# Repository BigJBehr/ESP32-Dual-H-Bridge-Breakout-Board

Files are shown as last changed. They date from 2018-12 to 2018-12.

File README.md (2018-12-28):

# ESP32 Dual H Bridge Breakout Board

This project is for an ESP32 Breakout board that was designed to be the brains of your next robot. The features of this board are;

Can accommodate any ESP32 dev kit that has two rows of up to twenty pins on one inch centers.
A place to mount a TB6612FNG dual H bridge DC motor controller daughter board.
A two screw terminal block for each motor connection.
A two screw terminal block and a set of five header pins for Vin & Gnd
Two rows of twenty GPIO breakout pins.
Headers for two HC-SR04 Sonar sensors, with voltage dividers on the Echo output.
A header for connecting to a tri-color, common anode, LED with limiting resistors.
On board 5V, 1A voltage regulator with five header pins for 5V & Gnd.
Four sets of headers for I2C connections with 3.3V & Gnd for each connection.
All components mount on one side of the circuit board.
The physical size of the board is 90mm x 56mm, two sided. This puts it well within the 100mm x 100mm size limits for most board makers low cost prototypes.

The board was designed around the DOIT ESP32 DEVKIT V1 which has two rows of eighteen pins each. Easily cut traces on the backside of the board allow you to separate the dedicated 5V, Gnd and 3.3V pins from their respective buses. Then you can use the pins in these locations as GPIO and using jumpers, connect the 5V, Gnd and 3.3V buses to the appropriate pins on the ESP32 dev kit that you are using.

The board was created using Kicad Ver 4.0.7.

## The files
ESP32_Robot_Bd.zip - This is all of the files needed to have the board fabricated. Send this file to your board manufacturer.

ESP32_Robot_Bd.kicad.pcb   - This is the kicad pcb file.

ESP32_Robot_Bd.net         - This is the kicad generated net file for the pcb.

ESP32_Robot_Bd.pdf         - This is a pdf version of the schematic.

ESP32_Robot_Bd.pro         - This is the kicad project.

ESP32_Robot_Bd.sch         - This is the kicad schematic.

ESP32_Robot_Bd-cache.lib   - This is the cached library. It has any custom library parts.

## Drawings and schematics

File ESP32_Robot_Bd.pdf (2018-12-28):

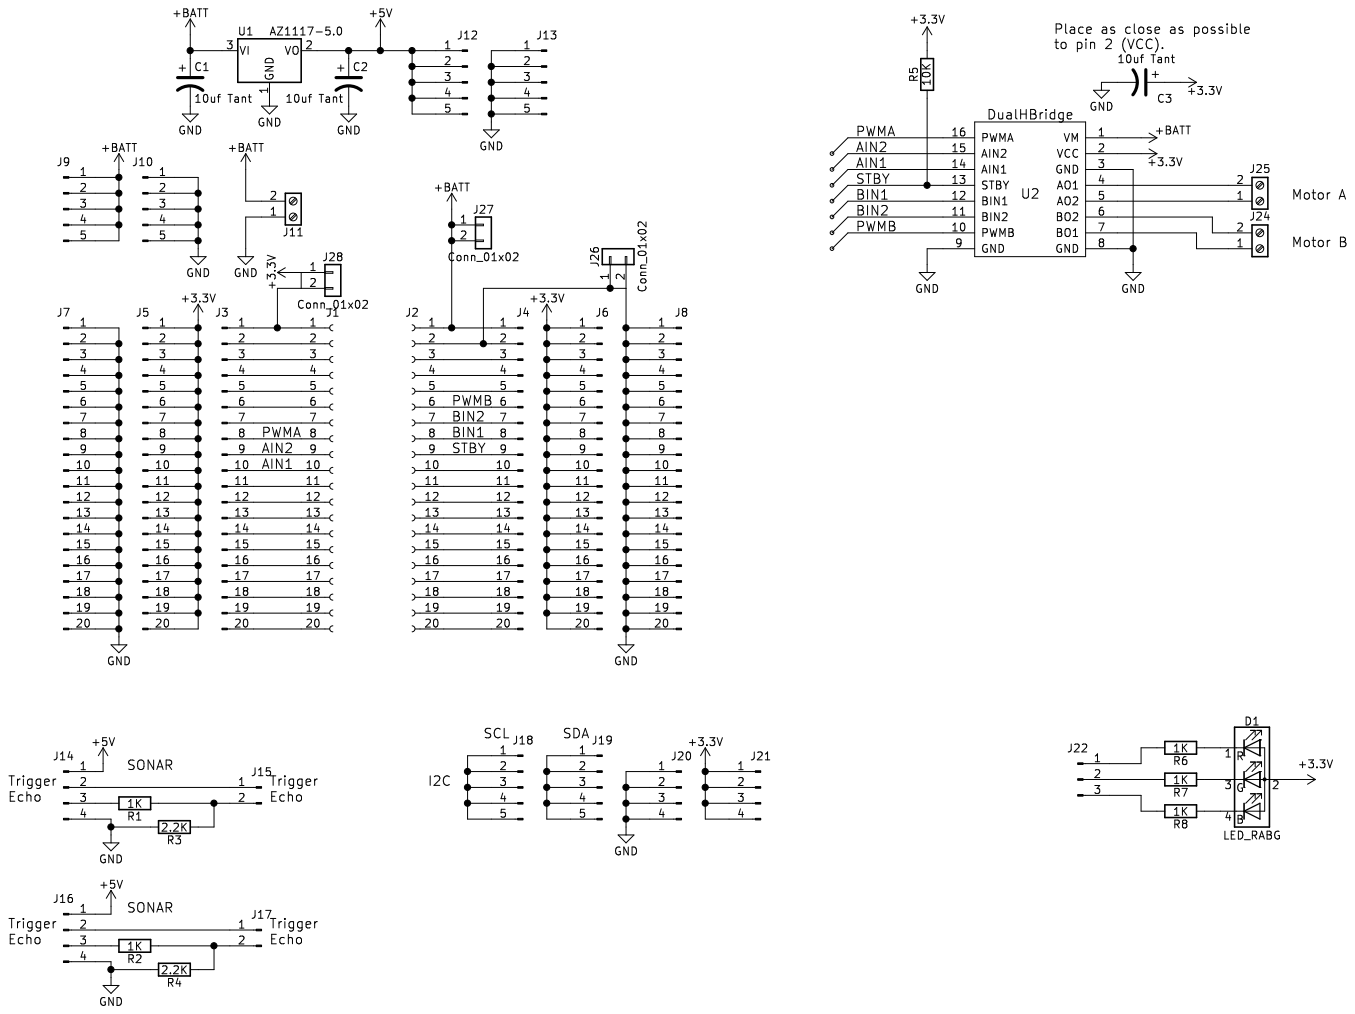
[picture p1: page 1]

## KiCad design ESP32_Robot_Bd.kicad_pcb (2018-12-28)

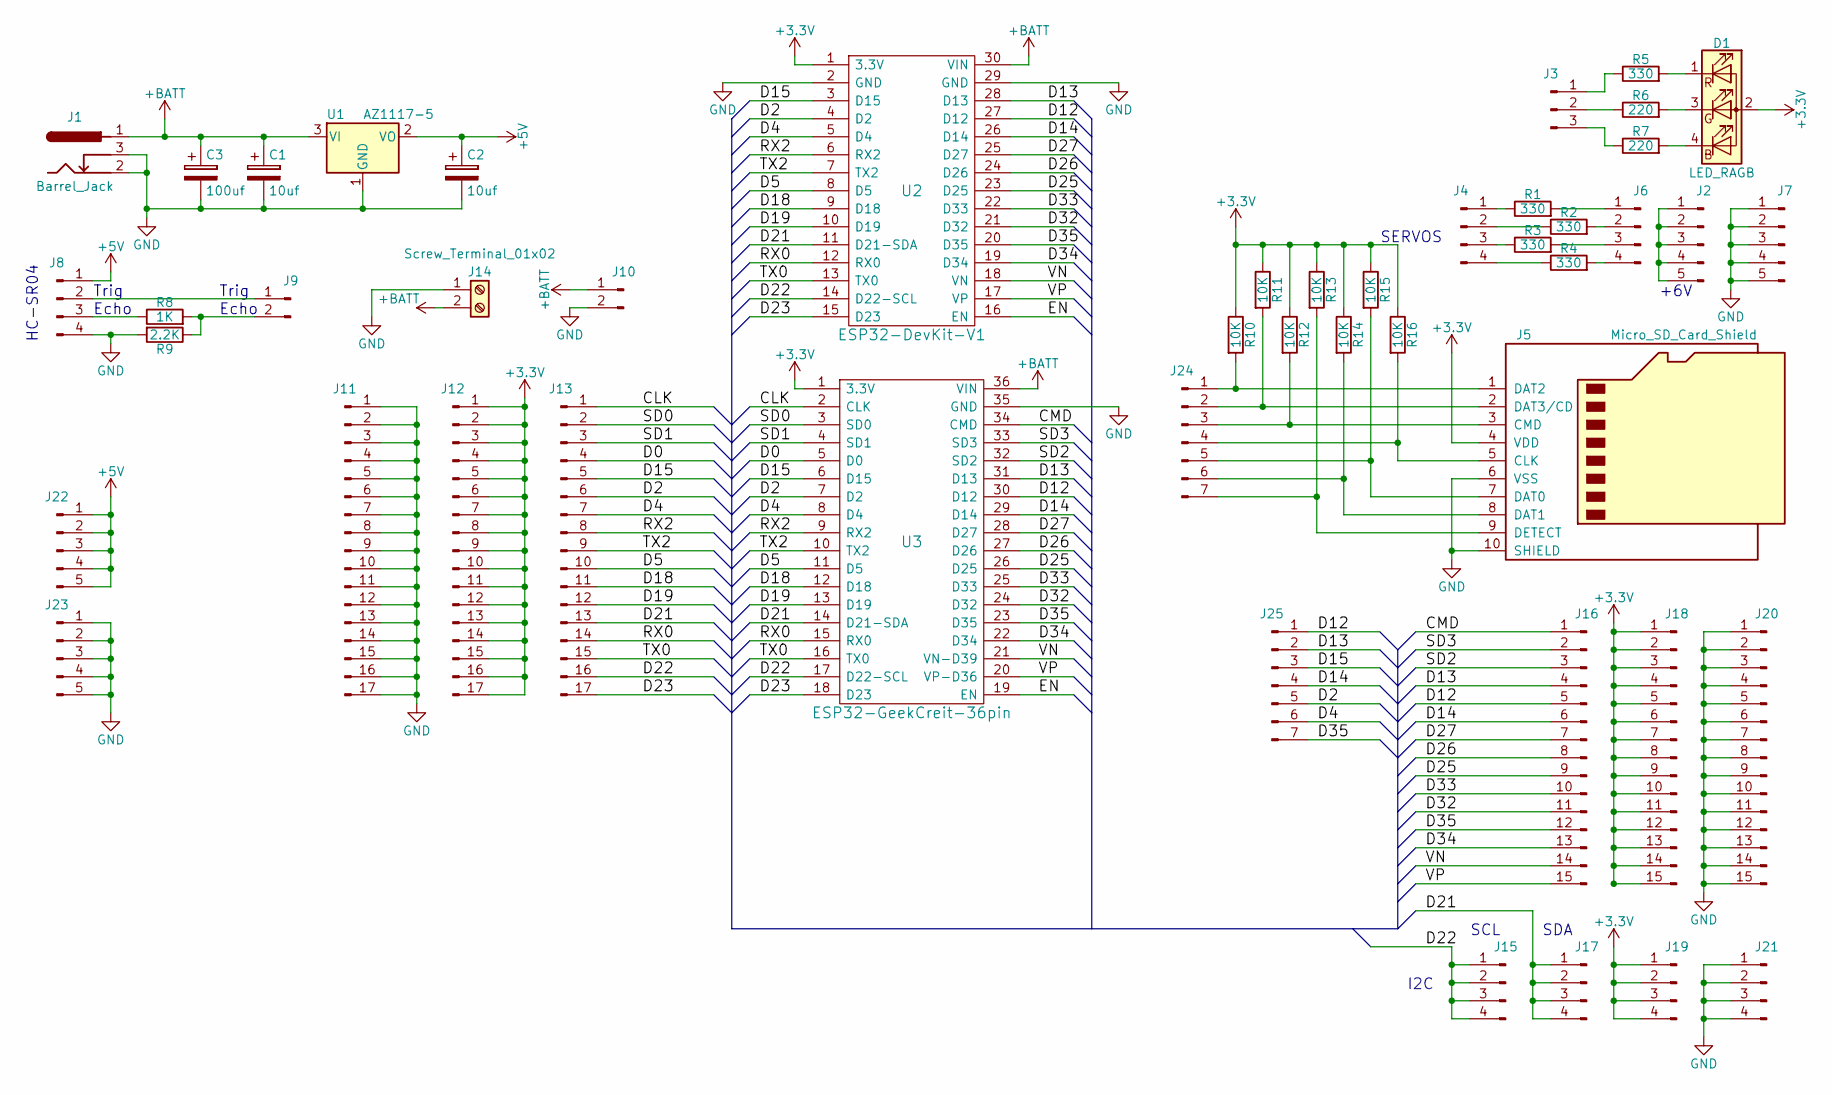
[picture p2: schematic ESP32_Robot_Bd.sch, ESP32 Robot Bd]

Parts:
C1, C2: 10uf; CP_Tantalum_Case-B_EIA-3528-21_Hand
C3: 100uf; CP_Radial_D6.3mm_P2.50mm
D1: LED_RAGB; LED_D5.0mm-4
J1: Barrel_Jack; Barrel_Jack_CUI_PJ-102AH
J2, J7, J22, J23: Conn_01x05_Male; Pin_Header_Straight_1x05_Pitch2.54mm
J3: Conn_01x03_Male; Pin_Header_Straight_1x03_Pitch2.54mm
J4, J6, J8, J15, J17, J19, J21: Conn_01x04_Male; Pin_Header_Straight_1x04_Pitch2.54mm
J5: Micro_SD_Card_Shield; uSD_Card_Receptacle
J9, J10: Conn_01x02_Male; Pin_Header_Straight_1x02_Pitch2.54mm
J11, J12, J13: Conn_01x17_Male; Pin_Header_Straight_1x17_Pitch2.54mm
J14: Screw_Terminal_01x02; TERMINAL_BLK-2
J16, J18, J20: Conn_01x15_Male; Pin_Header_Straight_1x15_Pitch2.54mm
J24, J25: Conn_01x07_Male; Pin_Header_Straight_1x07_Pitch2.54mm
R1, R2, R3, R4, R5: 330; R_1206_HandSoldering
R6, R7: 220; R_1206_HandSoldering
R8: 1K; R_1206_HandSoldering
R9: 2.2K; R_1206_HandSoldering
R10, R11, R12, R13, R14, R15, R16: 10K; R_1206_HandSoldering
U1: AZ1117-5; SOT-223-3_TabPin2
U2: ESP32-DevKit-V1; ESP32-30
U3: ESP32-GeekCreit-36pin; ESP32-36-LONGPADS

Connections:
+3V3: D1.2 (A), J5.4 (VDD), J12.1, J12.2, J12.3, J12.4, J12.5, J12.6, J12.7, J12.8, J12.9, J12.10, J12.11, J12.12, J12.13, J12.14, J12.15, J12.16, J12.17, J18.1, J18.2, J18.3, J18.4, J18.5, J18.6, J18.7, J18.8, J18.9, J18.10, J18.11, J18.12, J18.13, J18.14, J18.15, J19.1, J19.2, J19.3, J19.4, R10.1, R11.1, R12.1, R13.1, R14.1, R15.1, R16.1, U2.1 (3.3V), U3.1 (3.3V)
+5V: C2.1, J8.1, J22.1, J22.2, J22.3, J22.4, J22.5, U1.2 (VO)
+BATT: C1.1, C3.1, J1.1, J10.1, J14.2, U1.3 (VI), U2.30 (VIN), U3.36 (VIN)
/CLK: J13.1, U3.2 (CLK)
/CMD: J16.1, U3.34 (CMD)
/D0: J13.4, U3.5 (D0)
/D2: J13.6, J25.5, U2.4 (D2), U3.7 (D2)
/D4: J13.7, J25.6, U2.5 (D4), U3.8 (D4)
/D5: J13.10, U2.8 (D5), U3.11 (D5)
/D12: J16.5, J25.1, U2.27 (D12), U3.30 (D12)
/D13: J16.4, J25.2, U2.28 (D13), U3.31 (D13)
/D14: J16.6, J25.4, U2.26 (D14), U3.29 (D14)
/D15: J13.5, J25.3, U2.3 (D15), U3.6 (D15)
/D18: J13.11, U2.9 (D18), U3.12 (D18)
/D19: J13.12, U2.10 (D19), U3.13 (D19)
/D21: J13.13, J17.1, J17.2, J17.3, J17.4, U2.11 (D21-SDA), U3.14 (D21-SDA)
/D22: J13.16, J15.1, J15.2, J15.3, J15.4, U2.14 (D22-SCL), U3.17 (D22-SCL)
/D23: J13.17, U2.15 (D23), U3.18 (D23)
/D25: J16.9, U2.23 (D25), U3.26 (D25)
/D26: J16.8, U2.24 (D26), U3.27 (D26)
/D27: J16.7, U2.25 (D27), U3.28 (D27)
/D32: J16.11, U2.21 (D32), U3.24 (D32)
/D33: J16.10, U2.22 (D33), U3.25 (D33)
/D34: J16.13, U2.19 (D34), U3.22 (D34)
/D35: J16.12, J25.7, U2.20 (D35), U3.23 (D35)
/EN: U2.16 (EN), U3.19 (EN)
/RX0: J13.14, U2.12 (RX0), U3.15 (RX0)
/RX2: J13.8, U2.6 (RX2), U3.9 (RX2)
/SD0: J13.2, U3.3 (SD0)
/SD1: J13.3, U3.4 (SD1)
/SD2: J16.3, U3.32 (SD2)
/SD3: J16.2, U3.33 (SD3)
/TX0: J13.15, U2.13 (TX0), U3.16 (TX0)
/TX2: J13.9, U2.7 (TX2), U3.10 (TX2)
/VN: J16.14, U2.18 (VN), U3.21 (VN-D39)
/VP: J16.15, U2.17 (VP), U3.20 (VP-D36)
GND: C1.2, C2.2, C3.2, J1.2, J1.3, J5.6 (VSS), J5.10 (SHIELD), J7.1, J7.2, J7.3, J7.4, J7.5, J8.4, J10.2, J11.1, J11.2, J11.3, J11.4, J11.5, J11.6, J11.7, J11.8, J11.9, J11.10, J11.11, J11.12, J11.13, J11.14, J11.15, J11.16, J11.17, J14.1, J20.1, J20.2, J20.3, J20.4, J20.5, J20.6, J20.7, J20.8, J20.9, J20.10, J20.11, J20.12, J20.13, J20.14, J20.15, J21.1, J21.2, J21.3, J21.4, J23.1, J23.2, J23.3, J23.4, J23.5, R9.2, U1.1 (GND), U2.2 (GND), U2.29 (GND), U3.35 (GND)
unnamed: D1.1 (RK), R5.2
unnamed: D1.3 (GK), R6.2
unnamed: D1.4 (BK), R7.2
unnamed: J2.1, J2.2, J2.3, J2.4, J2.5
unnamed: J3.1, R5.1
unnamed: J3.2, R6.1
unnamed: J3.3, R7.1
unnamed: J4.1, R1.1
unnamed: J4.2, R2.1
unnamed: J4.3, R3.1
unnamed: J4.4, R4.1
unnamed: J6.1, R1.2
unnamed: J6.2, R2.2
unnamed: J6.3, R3.2
unnamed: J6.4, R4.2
unnamed: J8.2, J9.1
unnamed: J8.3, R8.1
unnamed: J9.2, R8.2, R9.1
unnamed: J5.1 (DAT2), J24.1, R10.2
unnamed: J5.2 (DAT3/CD), J24.2, R11.2
unnamed: J5.3 (CMD), J24.3, R12.2
unnamed: J5.5 (CLK), J24.4, R16.2
unnamed: J5.7 (DAT0), J24.5, R15.2
unnamed: J5.8 (DAT1), J24.6, R14.2
unnamed: J5.9 (DETECT), J24.7, R13.2

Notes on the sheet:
Echo
Trig
HC-SR04
SDA
SCL
I2C
SERVOS
+6V

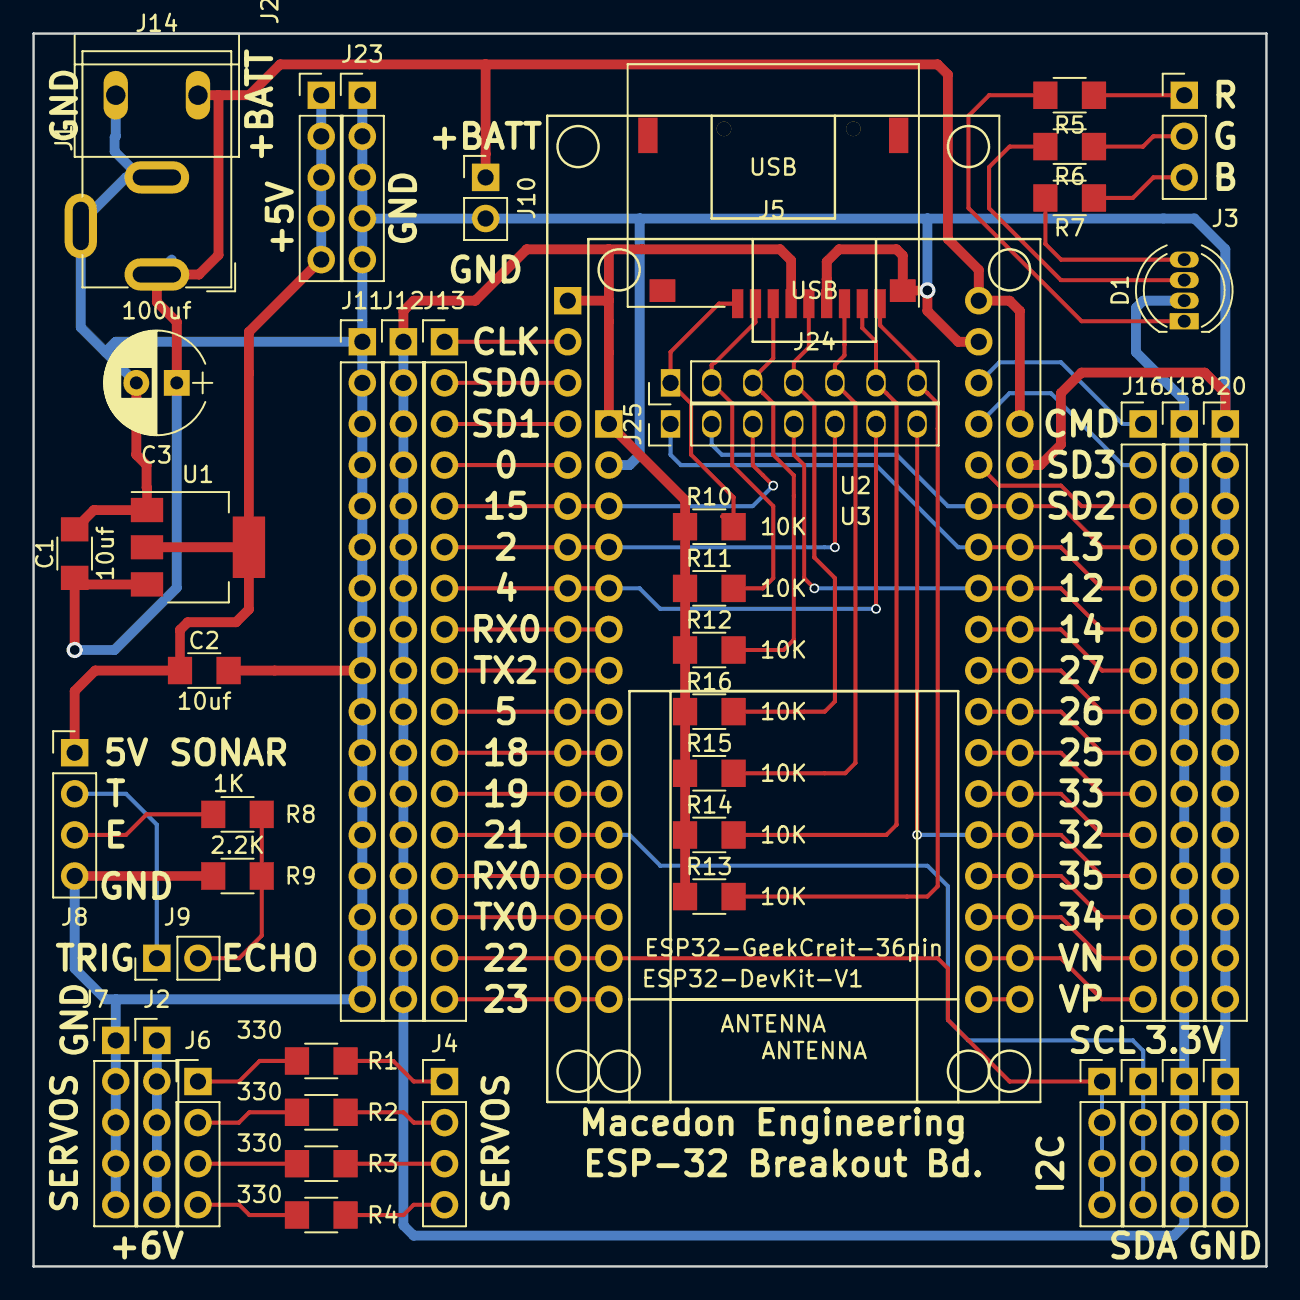
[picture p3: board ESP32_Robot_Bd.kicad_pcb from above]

Board: 2 copper layers, 76.2 x 76.2 mm, 48 parts (0 on the bottom side), 62 nets.
